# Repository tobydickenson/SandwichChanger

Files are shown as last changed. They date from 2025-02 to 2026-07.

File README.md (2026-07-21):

# Tool changer for CP40 nozzle tips

This is a CP40 nozzle holder, sized for lumenpnp. Differences from the original lumenpnp tool changer include:
- Lower profile, for maximum Safe-Z clearance. The nozzle tips are mounted as low as possible; any lower and the nozzle would not be able to pick them up.
- Sprung clips for retaining the nozzle tips in position, for smoother faster tip changes.
- The tip retention mechanism is printed with no bridging or overhangs, for maximum precision.
- All slots are equivalent. Tips can be loaded in any order.
- Slightly higher density. This holds 7 nozzle tips in the same space that the lumenpnp uses to hold 6.
- Vision-friendly, particularly if the top, bottom, and mounting layers are printed in contrasting color.

The tool changer is printed in 4 parts:
- Top layer. The large flange of the CP40 nozzle tip presses down onto the top layer for precise control of tip loading Z position.
- Middle layer. This is the sprung clamp. The top and middle layer cradle and support the nozzle tip shaft for precise control of the X/Y position.
- Bottom layer. This fits into the narrow part of the tip. The nozzle pulls against this layer during extraction.
- Mounting layer. This layer contains the build plate mounting features.

The 4 parts are clamped together with 8x 16mm M3 bolts and nuts. It is best to insert a couple of nozzle tips into the holder before tightening these nuts to ensure that all parts are aligned.

## Printing

The top 3 parts are obviously printed flat. The mounting part is best printed on its back.

The photos show multiple colors, but of course the tool changer is fully functional printed all in the same material.

I normally print in PETG, but any regular filament is fine.

## Recommended Automatic Tip Changer Motion Sequence

1. Start above the changing station. It is important to capture the X/Y coordinate precisely to ensure that the nozzle will be aligned with the tip during the loading operation. I find the best way to capture the X/Y coordinate is using top vision, with a medium size tool in the changer. The tip internal hole will be out of focus, but sufficiently visible for alignment purposes.
2. The second location is at the same X/Y coordinate as the first, but with the Z lowered so that the nozzle spring is fully compressed and the tip fully driven onto nozzle. NB all of the force of compressing the spring is carried by the large flange onto the top surface of the tool changer.
3. The third location is at the same X/Y coordinate as the first, but with the nozzle spring having maybe 0.2mm compression so that the large flange is gently held against the top surface.
4. The fourth location is a 10mm movement in X/Y and maybe 0.4mm above the third location in Z. The movement from 4 to 3 should be a gentle landing of the large flange onto the top surface.

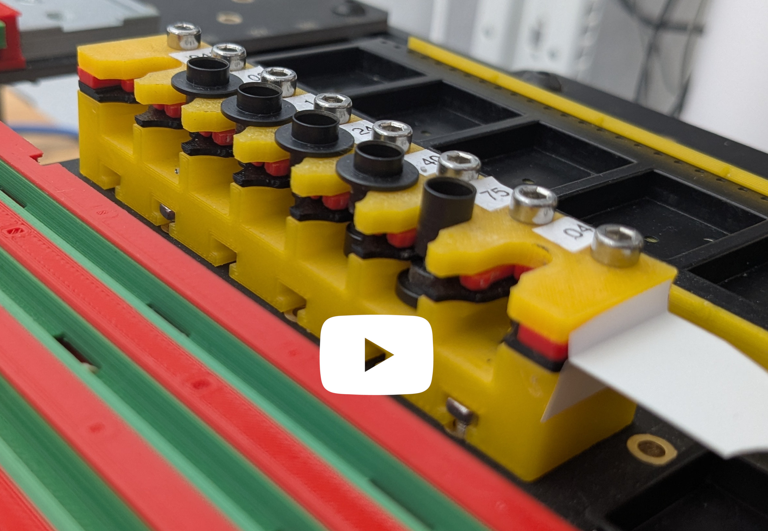
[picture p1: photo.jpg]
CP40 tool Changer Photo (https://www.youtube.com/watch?v=uOaBIDkO-QQ)


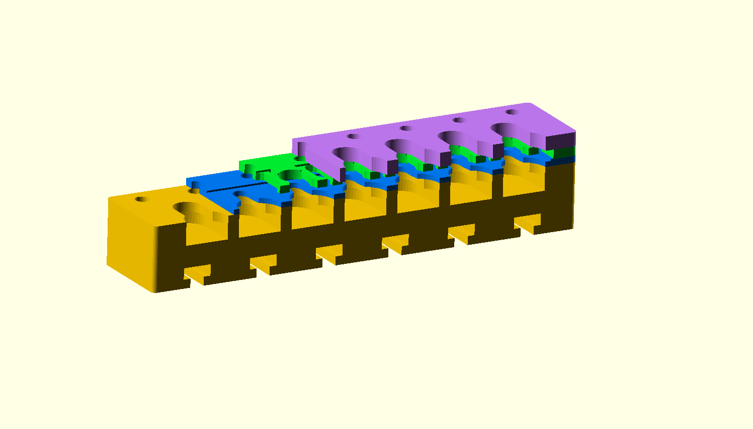
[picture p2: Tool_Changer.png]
CP40 tool Changer


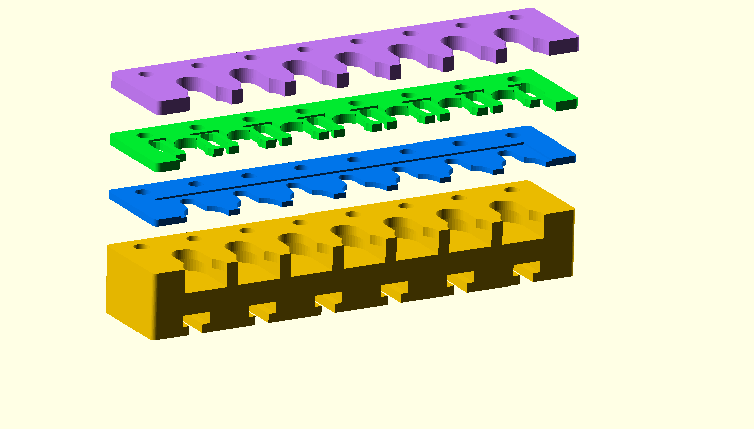
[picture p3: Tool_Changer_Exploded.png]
CP40 tool Changer Exploded


## Recommended Installation on lumpenpn

On a lumenpnp I recommend using an extra "build plate foot". This is the pillar which supports the middle of a secondary build plate.
Mount it directly underneath the tool changer to carry the vertical force when loading a nozzle tip.
This prevents the build plate flexing. Note that this needs to be installed before the toolchanger.

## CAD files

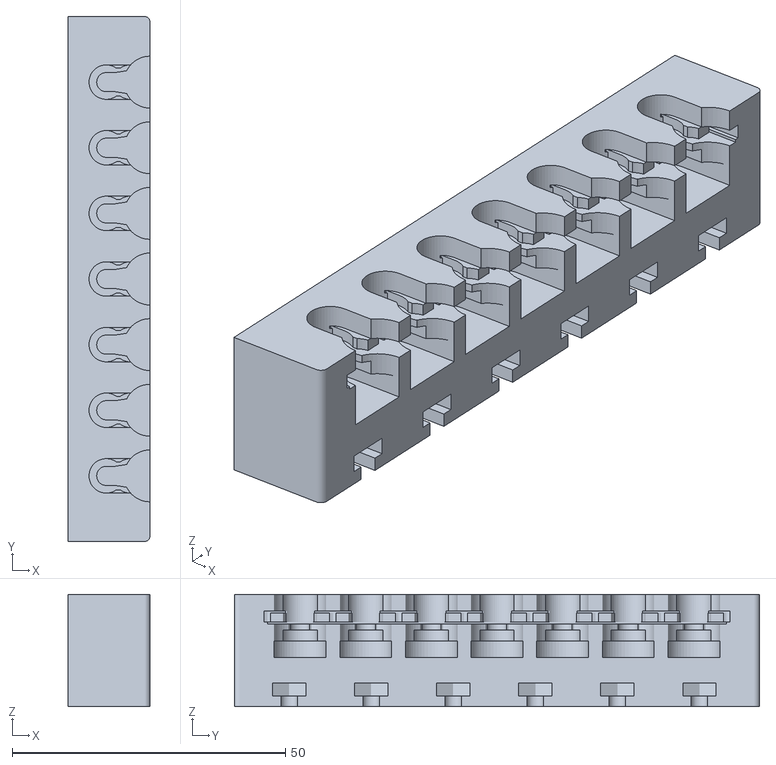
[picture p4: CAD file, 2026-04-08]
Tool_Changer_all_in_one__not_recommended.stl
15.0 x 96.0 x 20.5

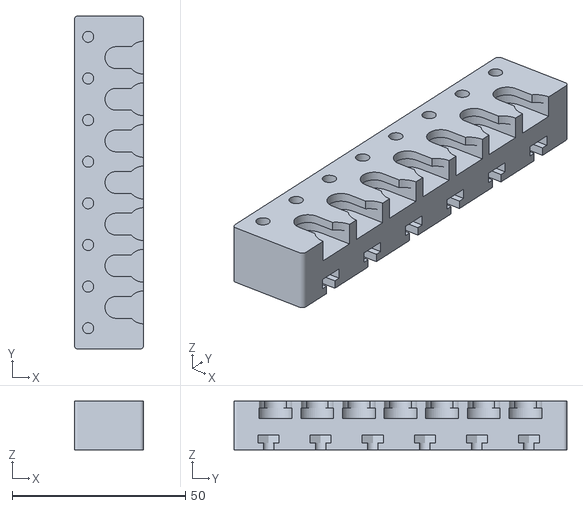
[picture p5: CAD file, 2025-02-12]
Tool_Changer_Mount.stl
20.0 x 96.0 x 14.0

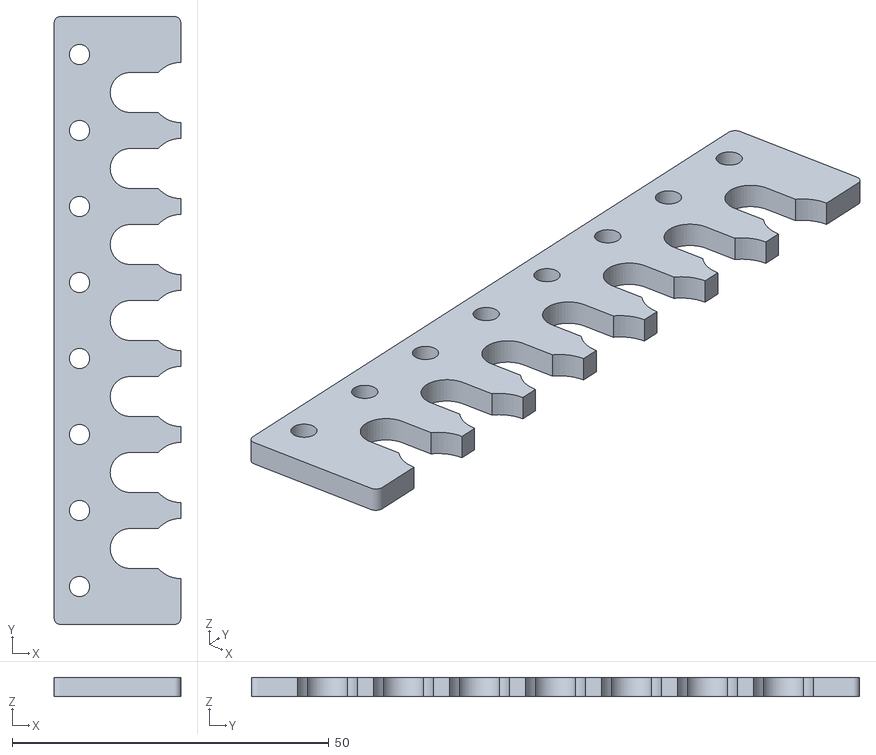
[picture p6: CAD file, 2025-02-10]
Tool_Changer_Top.stl
20.0 x 96.0 x 3.00

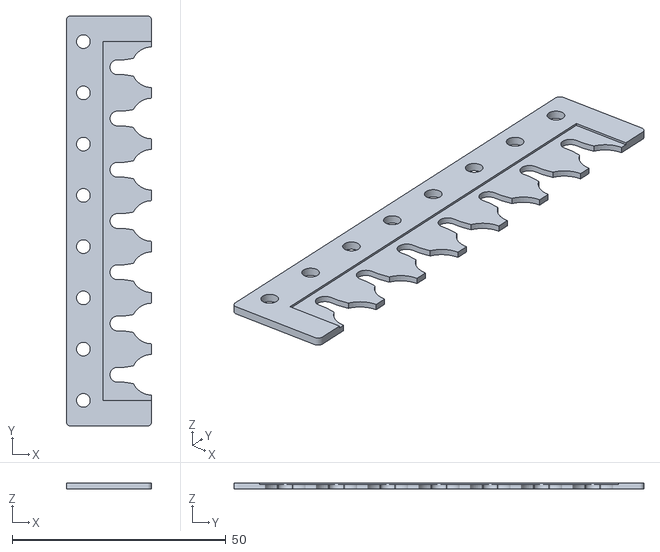
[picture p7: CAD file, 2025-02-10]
Tool_Changer_Bottom.stl
20.0 x 96.0 x 1.50

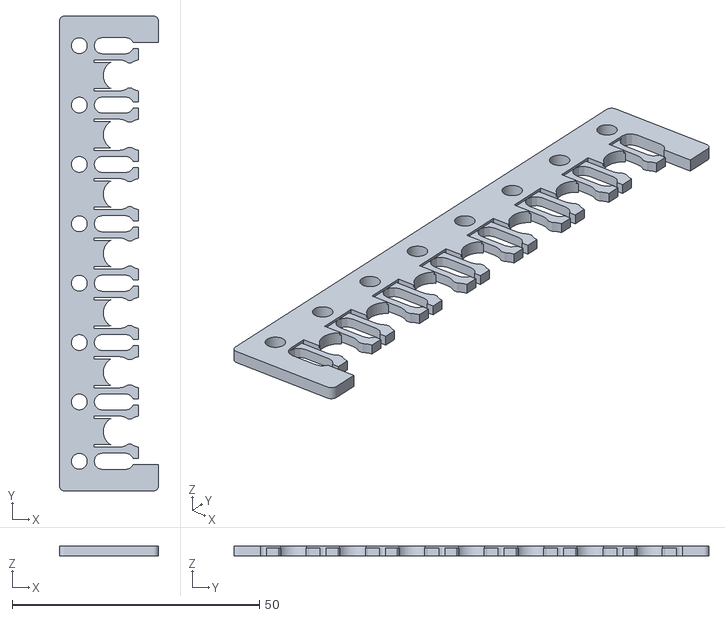
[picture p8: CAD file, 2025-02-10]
Tool_Changer_Middle.stl
20.0 x 96.0 x 2.00

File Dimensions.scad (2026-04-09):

// Radius of nozzle tip where it is held in the slot
r = 3.5 / 2;

// Close fit radius of the nozzle tip shank
or = 6.3 / 2;

// center point of nozzle when held
q = 12;


// Clearance radius for the widest tool
tr = 9.5 / 2;

// Width of nozzle holder
w = 20;

// Border size
b = 6;

// Distance between nozzles
d = 12;

// The gap between adjacent layers to allow for movement
gap = 0.4;

// Number of nozzles
nozzles = 7;

screw_holes_for_holding_all_layers_together = true;

back_remove_thickness = screw_holes_for_holding_all_layers_together ? 0.0 : 5.0;


// Optionally peel back some layers to show inner working
cutaway_visualisation = 0;

e = 0.01;

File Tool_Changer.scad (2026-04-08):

// Total view of the three layers
// Not for printing but for visiaulisation

offset = 10.0; // [0:0.01:20.0]

translate([0, 0, 3.5+2*offset]) color([0.8, 0.5, 1])  { include <Tool_Changer_Top.scad> }

translate([0, 0, 1.5+1*offset]) color([0, 1, 0.2]) { include <Tool_Changer_Middle.scad> }

translate([0, 0, 0]) color([0, 0.5, 1])  { include <Tool_Changer_Bottom.scad> }

translate([0, 0, -14-1*offset]) color([1, 0.8, 0]) { include <Tool_Changer_Mount.scad> }

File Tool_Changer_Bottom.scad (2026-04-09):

include <Dimensions.scad>

intersection()
{
    $fn = 48;

    // Nozzle slot thickness
    s = 1.1;

    // center point
    q = 12;

    h = s+gap;

    difference()
    {
        union()
        {
            linear_extrude(h) offset(1) offset(-1) square([w, nozzles * d + 2 * b]);
        }
        // Slot for nozzle slit
        for(i = [1:nozzles])
        {
            hull()
            {
                translate([q, b + d/2 + (i - 1) * d, -e]) cylinder(h + 2*e, r, r);
                translate([w + q, b + d/2 + (i - 1) * d, -e]) cylinder(h + 2*e, r, r);
            }
            translate([w, b + d/2 + (i - 1) * d, -e]) cylinder(h + 2*e, tr, tr);
            
            // lead in
            hull()
            {
                translate([w-tr+r, b + d/2 + (i - 1) * d, -e]) cylinder(h + 2*e, r+0.5, r+0.5);
                translate([q+r, b + d/2 + (i - 1) * d, -e]) cylinder(h + 2*e, r, r);
            }
            
            // slice down to the right thickness for the nozzle slot
            translate([q-or-0.2, b + d/2 + (i - 1) * d - d/2, s]) cube([20, d+e, 10], false);
        }

        if(screw_holes_for_holding_all_layers_together)
        for(i = [-1:nozzles + 1])
        {
            translate([w - 16, b + d + (i - 1) * d, -e]) cylinder(h + 2*e, 1.6, 1.6);
        }

        // If we have wide border, then add a through hole. Default parameters above do not
        if(b>8)
        {
            translate([w / 2, b / 2, -e]) cylinder(h + 2*e, 2.2, 2.2);
            translate([w / 2, nozzles * d + 2 * b - b / 2, -e]) cylinder(h + 2*e, 2.2, 2.2);
        }

        if(cutaway_visualisation)
        {
            translate([0,0,-1]) linear_extrude(h+2) offset(e) square([w, 1*d + b]);
        }

        // If we dont have the screw holes, then we can remove some material from the back
        if(back_remove_thickness>0)
        {
            translate([-e,-e,-e])
            linear_extrude(h+e+e) square([back_remove_thickness+e, nozzles * d + 2 * b + 2*e]);
        }
    }
}

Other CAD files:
Tool_Changer_Middle.scad
Tool_Changer_Mount.scad
Tool_Changer_Top.scad

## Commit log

2024-10-08 imported from https://github.com/richardklingler/openpnp/tree/master/openscad/toolchanger
    [Tool_Changer.scad, Tool_Changer_Bottom.scad, Tool_Changer_Middle.scad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]
2024-10-08 first changes for lumenpnp format
    [Tool_Changer.scad, Tool_Changer_Bottom.scad, Tool_Changer_Middle.scad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]
2024-10-08 z stack tidy up
    [Tool_Changer.scad, Tool_Changer_Middle.scad, Tool_Changer_Top.scad]
2024-10-08 a day of tweaking
    [Tool_Changer.scad, Tool_Changer_Bottom.scad, Tool_Changer_Bottom.stl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]
2024-10-09 its too short for the head!
    [Tool_Changer.scad, Tool_Changer_Bottom.scad, Tool_Changer_Bottom.stl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]
2024-10-09 filament reduction
    [Tool_Changer_Mount.scad, Tool_Changer_Mount.stl]
2024-10-10 commentry. parameteris slots
    [Tool_Changer_Bottom.scad, Tool_Changer_Middle.scad, Tool_Changer_Mount.scad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]
2024-10-10 Added dimensions file
    [Dimensions.scad, Tool_Changer.scad, Tool_Changer_Bottom.scad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]
2024-10-10 better dimensions
    [Dimensions.scad, Tool_Changer_Bottom.scad, Tool_Changer_Middle.scad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]
2025-02-12 that was too short
    [Tool_Changer.scad, Tool_Changer_Mount.scad, Tool_Changer_Mount.stl]
2025-08-18 changes before publishing
    [Dimensions.scad, Tool_Changer.scad, Tool_Changer_Bottom.scad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]
2026-04-08 fix gap
    [Tool_Changer.scad]
2026-04-08 normally this is printed in multiple sections then bolted together. This adds an option to print all in one
    [Tool_Changer_all_in_one__not_recommended.stl]
